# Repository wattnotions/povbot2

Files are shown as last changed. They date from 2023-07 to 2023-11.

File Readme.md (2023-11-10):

# POVbot - A Small Pi Zero FPV Robot



## 3d Print Files

Look in 3d_print folder to find a 3mf file with the chassis , camera holder and wheels ready to print.



## Software

Setting up video streaming and remote control is very easy.

Clone this repo to a raspberry pi, navigate to web_server/keyandvid/

From there run "python app.py" and the web server will start

Then you can navigate to your pis ip address using a computer on the same wifi. Use port 8000.

For example : 192.168.0.186:8000 and you should see your video stream. The robot can be steered using the WASD keys on your keyboard



## PCB Files

The hat was designed in Kicad 7. All project files are in kicad_files.

The board was made and assembled by PCBway. If you wish to get your own board assembled using PCBway look in kicad_files/pcbway_production for all of the required PCB manufacture and assembly files, ready for upload to JLCPCB.

## Youtube video

I made a short video explaining the project. It is available here:

[Watch the video](https://www.youtube.com/watch?v=tIp2PrZHXOc)

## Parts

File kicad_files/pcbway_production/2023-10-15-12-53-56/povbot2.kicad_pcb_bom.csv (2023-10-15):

designator | quantity | value | pack | mpn | mount_type
C1 | 1 | 22u | C_0603_1608Metric |  | smt
C10, C11, C12 | 3 | 22u | C_0805_2012Metric |  | smt
C13 | 1 | 10n | C_0603_1608Metric |  | smt
C2 | 1 | 0.1uF | C_0603_1608Metric |  | smt
C6, C7 | 2 | 4.7uF | C_0603_1608Metric |  | smt
C8, C9 | 2 | 10uF | C_0603_1608Metric |  | smt
D1 | 1 | LED | LED_0603_1608Metric |  | smt
D2, D3 | 2 | D_Schottky | D_SOD-323 | SBA120CS_R1_00001 | smt
J1 | 1 | GPIO | PinSocket_2x20_P2.54mm_Vertical | 61304021121 | tht
J4, J5, J6 | 3 | Conn_01x02 | JST_PH_B2B-PH-K_1x02_P2.00mm_Vertical | B2B-PH-K-S | tht
J7 | 1 | USB_B_Micro | USB_Micro-B_Molex_47346-0001 | 0473460001 | smt
L1 | 1 | 1uH | IND_SRP4020TA-1R0M | SRP4020TA-1R0M | smt
MH1, MH2, MH3, MH4 | 4 | MountingHole_2.7mm_M2.5 | MountingHole_2.7mm_M2.5 |  | tht
R1 | 1 | 1M | R_0603_1608Metric |  | smt
R5 | 1 | 470R | R_0603_1608Metric |  | smt
R6 | 1 | 2k | R_0603_1608Metric |  | smt
U1 | 1 | TPS61232DRC | Texas_S-PVSON-N10_ThermalVias | TPS61232DRCR | smt
U4 | 1 | MCP73831-2ACI_MC | SON50P200X300X100-9N | MCP73831-2ACI/MC | tht
U5 | 1 | TB6612FNG | SSOP-24_5.3x8.2mm_P0.65mm | TB6612FNG,C,8,EL | smt

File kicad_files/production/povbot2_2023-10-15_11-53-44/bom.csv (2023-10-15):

Designator | Footprint | Quantity | Value | LCSC Part #
C1 | 0603 | 1 | 22u
C10, C11, C12 | 0805 | 3 | 22u
C13 | 0402 | 1 | 10n
C2 | 0603 | 1 | 0.1uF
C6, C7 | 0603 | 2 | 4.7uF
C8, C9 | 0603 | 2 | 10uF
D1 | 0402 | 1 | LED
D2, D3 | D_SOD-323 | 2 | D_Schottky | C146335
J1 | PinSocket_2x20_P2.54mm_Vertical | 1 | GPIO
J4, J5, J6 | JST_PH_B2B-PH-K_1x02_P2.00mm_Vertical | 3 | Conn_01x02
J7 | USB_Micro-B_Molex_47346-0001 | 1 | USB_B_Micro
L1 | 0402 | 1 | 1uH
R1 | 0603 | 1 | 1M
R5 | 0603 | 1 | 470R
R6 | 0603 | 1 | 2k
U1 | Texas_S-PVSON-N10_ThermalVias | 1 | TPS61232DRC
U4 | SON50P200X300X100-9N | 1 | MCP73831-2ACI_MC | C150772
U5 | SSOP-24_5.3x8.2mm_P0.65mm | 1 | TB6612FNG | C141517

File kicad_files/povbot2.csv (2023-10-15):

Id | Designator | Footprint | Quantity | Designation | Supplier and ref | Column1 | _1
1 | C1 | C_0603_1608Metric | 1 | 22u
2 | J5,J6,J4 | JST_PH_B2B-PH-K_1x02_P2.00mm_Vertical | 3 | Conn_01x02
3 | J1 | PinSocket_2x20_P2.54mm_Vertical | 1 | GPIO
4 | D1 | LED_0402_1005Metric | 1 | LED
5 | R1 | R_0603_1608Metric | 1 | 1M
6 | C12,C10,C11 | C_0805_2012Metric | 3 | 22u
7 | J7 | USB_Micro-B_Molex_47346-0001 | 1 | USB_B_Micro
8 | D3,D2 | D_SOD-323 | 2 | D_Schottky
9 | U1 | Texas_S-PVSON-N10_ThermalVias | 1 | TPS61232DRC
10 | R5 | R_0603_1608Metric | 1 | 470R
11 | U5 | SSOP-24_5.3x8.2mm_P0.65mm | 1 | TB6612FNG
12 | C13 | C_0402_1005Metric | 1 | 10n
13 | L1 | L_0402_1005Metric | 1 | 1uH
14 | C7,C6 | C_0603_1608Metric | 2 | 4.7uF
15 | R6 | R_0603_1608Metric | 1 | 2k
16 | C2 | C_0603_1608Metric | 1 | 0.1uF
17 | U4 | SON50P200X300X100-9N | 1 | MCP73831-2ACI_MC
18 | C9,C8 | C_0603_1608Metric | 2 | 10uF

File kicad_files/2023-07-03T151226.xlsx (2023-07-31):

Index | Quantity | Part Number | Manufacturer Part Number | Description | Customer Reference | Available | Backorder | Unit Price | Extended Price EUR
1 | 2 | 2007-BB-2020BGR-TRBCT-ND | BB-2020BGR-TRB | ADDRESS LED DISCRETE SERIAL RGB |  | 2 | 0 | 1.41 | 2.82
2 | 1 | 296-44498-1-ND | TPS61232DRCR | IC REG BOOST 5V 4A 10VSON |  | 1 | 0 | 2.56 | 2.56
3 | 1 | MCP73831T-2ACI/MCCT-ND | MCP73831T-2ACI/MC | IC BATT CONTRL LI-ION 1CELL 8DFN |  | 1 | 0 | 0.72 | 0.72
4 | 1 | TB6612FNGC8ELCT-ND | TB6612FNG,C,8,EL | IC MOTOR DRIVER 2.7V-5.5V 24SSOP |  | 1 | 0 | 1.84 | 1.84
5 | 1 | 38-1007-ND | D6505I | LASER DIODE 650NM 5MW TO18 |  | 1 | 0 | 11.09 | 11.09
6 | 1 | 1528-2688-ND | 3872 | 5V ELECTROMAGNET 2.5 KG HOLDING |  | 1 | 0 | 6.85 | 6.85
7 | 3 |  | 2132260210 | Molex clik mate smd ra 2 way
8 | 2 |  | 151350200 (https://www.digikey.ie/en/products/detail/molex/0151350200/6833461) | click mate pre made leads

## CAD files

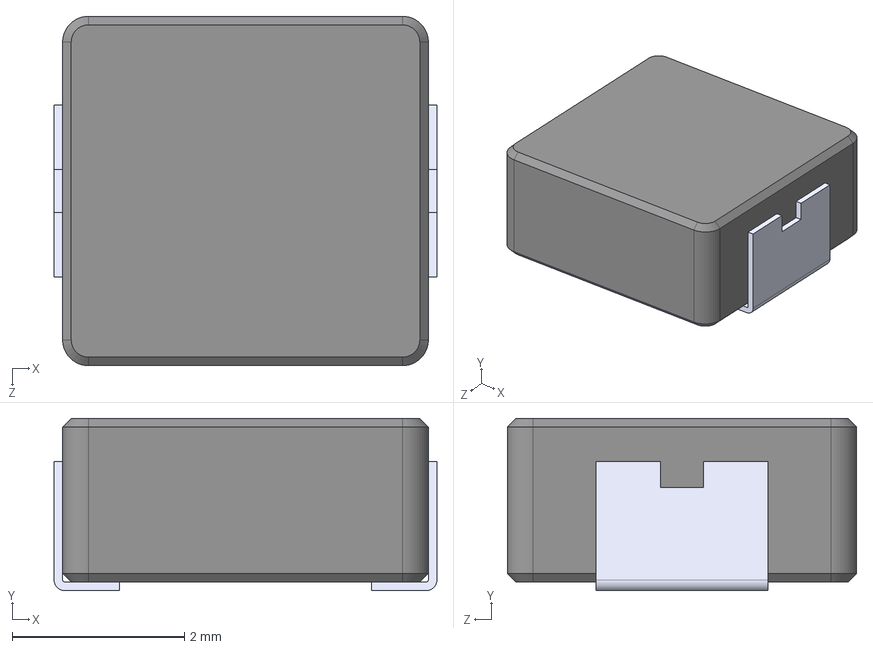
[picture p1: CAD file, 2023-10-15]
kicad_files/SRP4020TA-1R0M/SRP4020TA-1R0M.step
4.45 x 2.00 x 4.06 mm

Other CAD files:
3d_print/povbot_3d_print.3mf

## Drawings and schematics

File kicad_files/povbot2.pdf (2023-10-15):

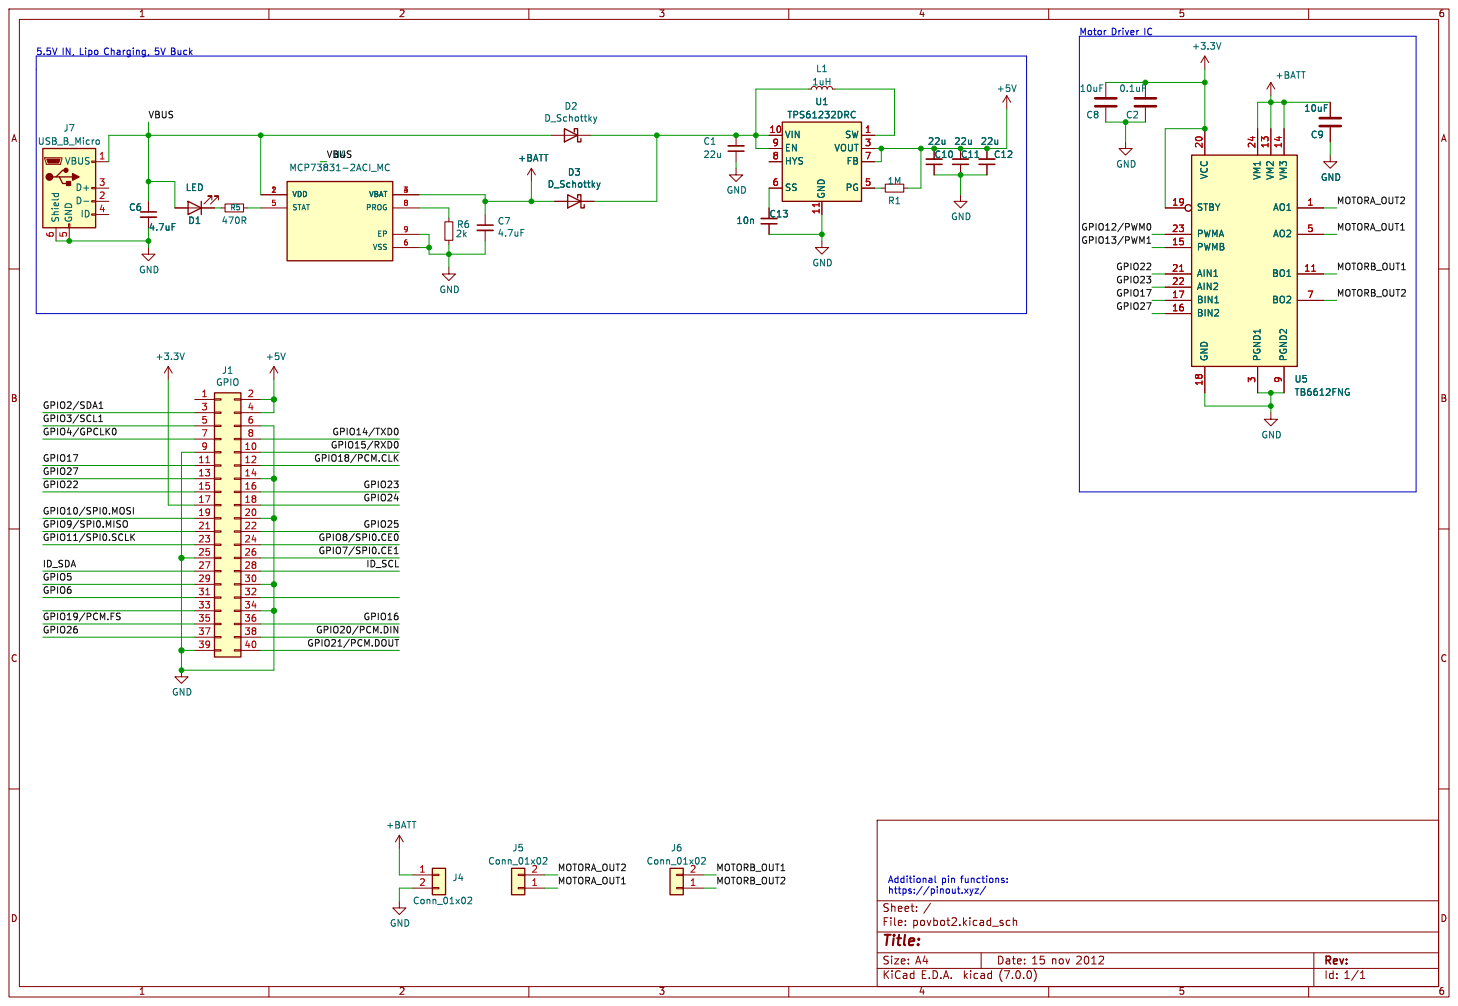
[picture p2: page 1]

Id: 1/1 Title: File: povbot2.kicad_sch Sheet: /

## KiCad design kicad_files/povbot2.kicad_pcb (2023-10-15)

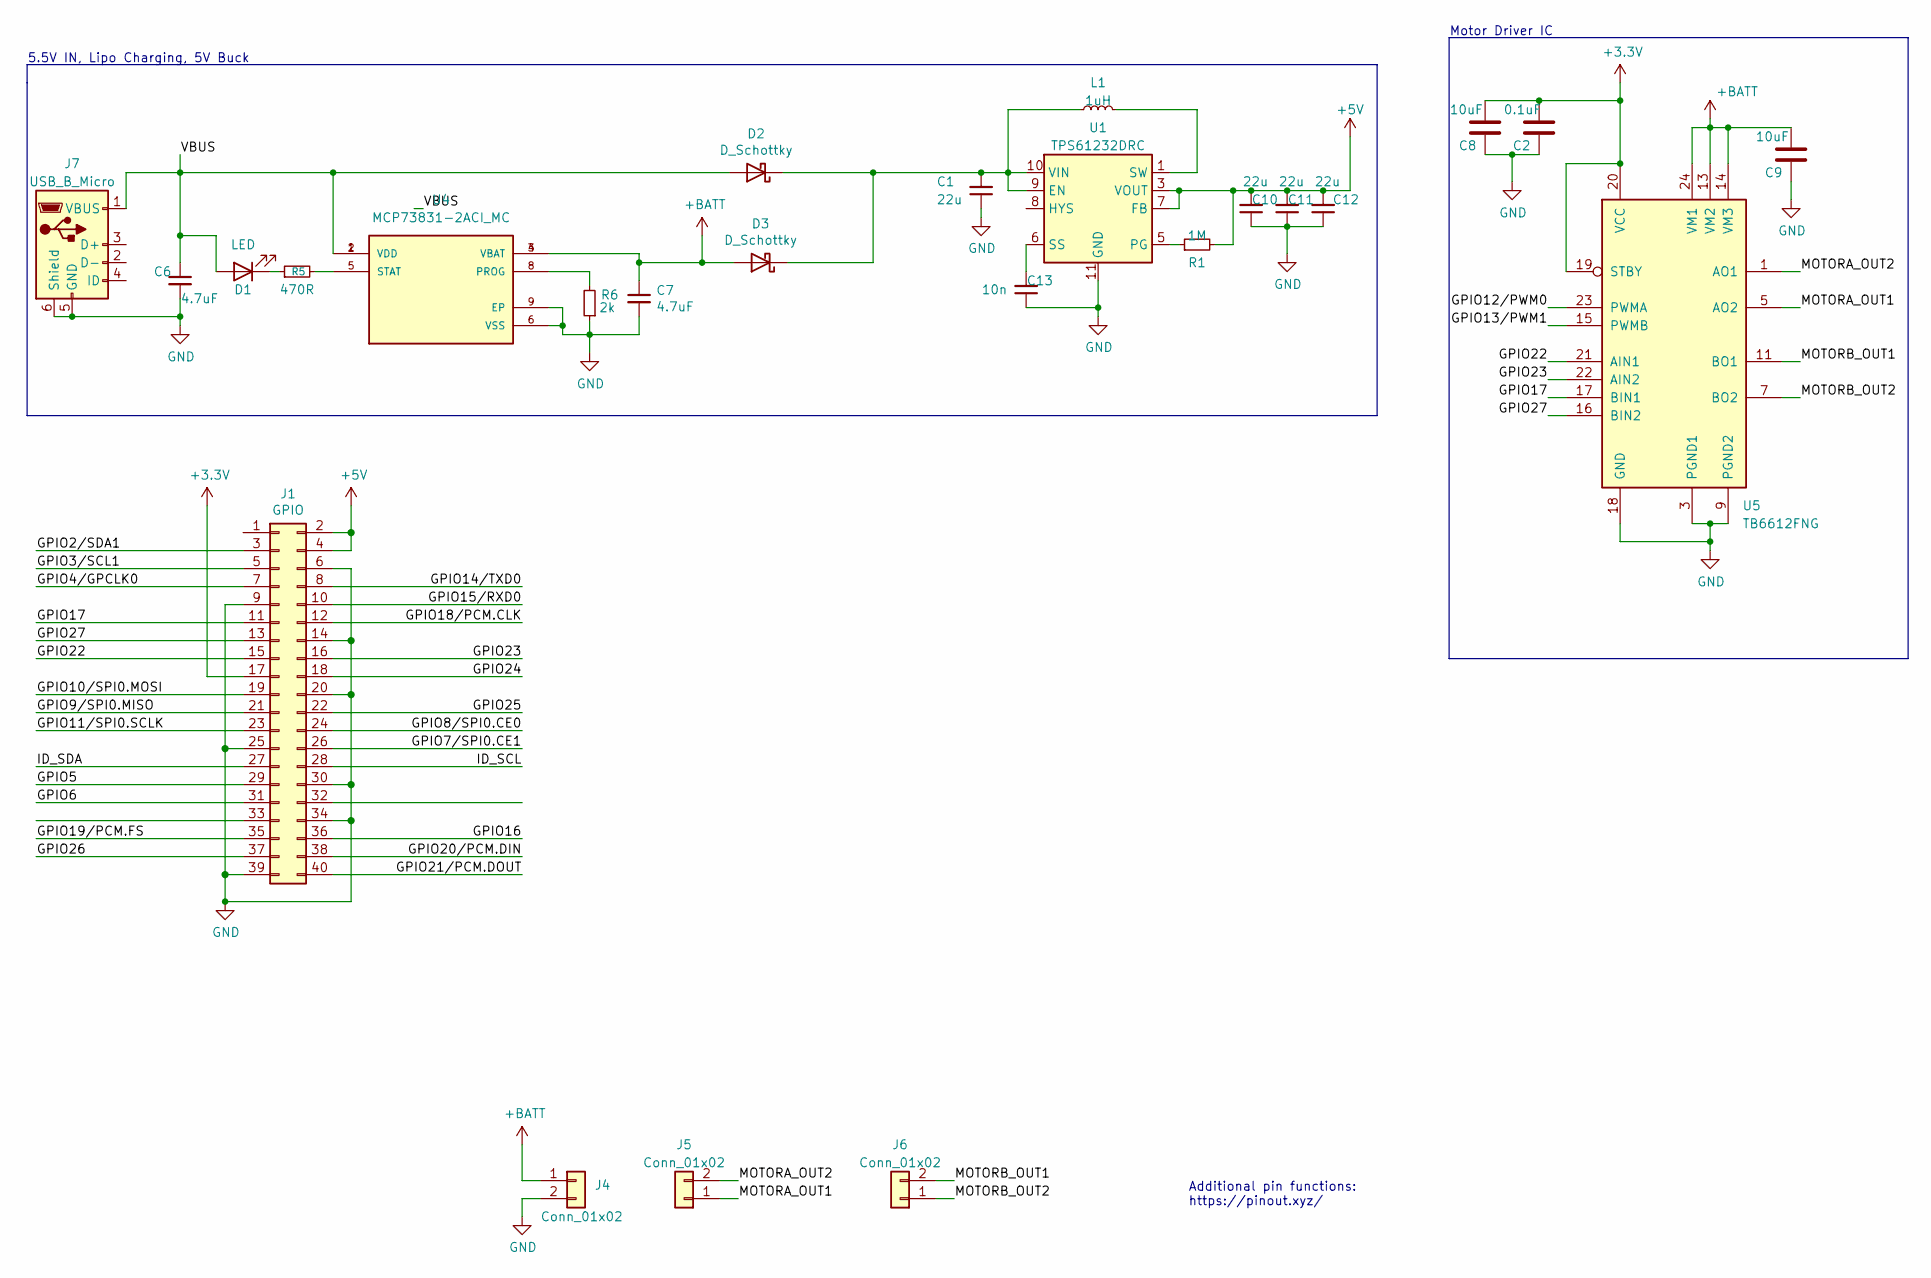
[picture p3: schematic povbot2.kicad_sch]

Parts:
C1: 22u; C_0603_1608Metric
C2: 0.1uF; C_0603_1608Metric
C6, C7: 4.7uF; C_0603_1608Metric
C8, C9: 10uF; C_0603_1608Metric
C10, C11, C12: 22u; C_0805_2012Metric
C13: 10n; C_0603_1608Metric
D1: LED; LED_0603_1608Metric
D2, D3: D_Schottky; D_SOD-323; MPN SBA120CS_R1_00001; LCSC C146335
J1: GPIO; PinSocket_2x20_P2.54mm_Vertical; MPN 61304021121
J4, J5, J6: Conn_01x02; JST_PH_B2B-PH-K_1x02_P2.00mm_Vertical; MPN B2B-PH-K-S
J7: USB_B_Micro; USB_Micro-B_Molex_47346-0001; MPN 0473460001
L1: 1uH; IND_SRP4020TA-1R0M; MPN SRP4020TA-1R0M
R1: 1M; R_0603_1608Metric
R5: 470R; R_0603_1608Metric
R6: 2k; R_0603_1608Metric
U1: TPS61232DRC; Texas_S-PVSON-N10_ThermalVias; MPN TPS61232DRCR
U4: MCP73831-2ACI_MC; SON50P200X300X100-9N; PARTREV G; LCSC C150772
U5: TB6612FNG; SSOP-24_5.3x8.2mm_P0.65mm; MPN TB6612FNG,C,8,EL; LCSC C141517

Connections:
+3V3: C2.1, C8.1, J1.17, U5.19 (STBY), U5.20 (VCC)
+5V: C10.2, C11.2, C12.2, J1.2, J1.4, R1.2, U1.3 (VOUT), U1.4 (VOUT), U1.7 (FB)
+BATT: C7.1, C9.1, D3.2 (A), J4.1, U4.3 (VBAT), U4.4 (VBAT), U5.13 (VM2), U5.14 (VM3), U5.24 (VM1)
/GPIO2/SDA1: J1.3
/GPIO3/SCL1: J1.5
/GPIO4/GPCLK0: J1.7
/GPIO5: J1.29
/GPIO6: J1.31
/GPIO7/SPI0.CE1: J1.26
/GPIO8/SPI0.CE0: J1.24
/GPIO9/SPI0.MISO: J1.21
/GPIO10/SPI0.MOSI: J1.19
/GPIO11/SPI0.SCLK: J1.23
/GPIO12/PWM0: U5.23 (PWMA)
/GPIO13/PWM1: U5.15 (PWMB)
/GPIO14/TXD0: J1.8
/GPIO15/RXD0: J1.10
/GPIO16: J1.36
/GPIO17: J1.11, U5.17 (BIN1)
/GPIO18/PCM.CLK: J1.12
/GPIO19/PCM.FS: J1.35
/GPIO20/PCM.DIN: J1.38
/GPIO21/PCM.DOUT: J1.40
/GPIO22: J1.15, U5.21 (AIN1)
/GPIO23: J1.16, U5.22 (AIN2)
/GPIO24: J1.18
/GPIO25: J1.22
/GPIO26: J1.37
/GPIO27: J1.13, U5.16 (BIN2)
/ID_SCL: J1.28
/ID_SDA: J1.27
/MOTORA_OUT1: J5.1, U5.5 (AO2), U5.6 (AO2)
/MOTORA_OUT2: J5.2, U5.1 (AO1), U5.2 (AO1)
/MOTORB_OUT1: J6.2, U5.11 (BO1), U5.12 (BO1)
/MOTORB_OUT2: J6.1, U5.7 (BO2), U5.8 (BO2)
/VBUS: C6.1, D1.2 (A), D2.2 (A), J7.1 (VBUS), U4.1 (VDD), U4.2 (VDD)
GND: C1.1, C2.2, C6.2, C7.2, C8.2, C9.2, C10.1, C11.1, C12.1, C13.1, J1.6, J1.9, J1.14, J1.20, J1.25, J1.30, J1.34, J1.39, J4.2, J7.5 (GND), J7.6 (Shield), R6.1, U1.11 (GND), U4.6 (VSS), U4.9 (EP), U5.3 (PGND1), U5.4 (PGND1), U5.9 (PGND2), U5.10 (PGND2), U5.18 (GND)
unnamed: D1.1 (K), R5.1
unnamed: C1.2, D2.1 (K), D3.1 (K), L1.1, U1.9 (EN), U1.10 (VIN)
unnamed: L1.2, U1.1 (SW), U1.2 (SW)
unnamed: R1.1, U1.5 (PG)
unnamed: C13.2, U1.6 (SS)
unnamed: R6.2, U4.8 (PROG)
unnamed: R5.2, U4.5 (STAT)

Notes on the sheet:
Motor Driver IC
5.5V IN, Lipo Charging, 5V Buck
Additional pin functions: https://pinout.xyz/

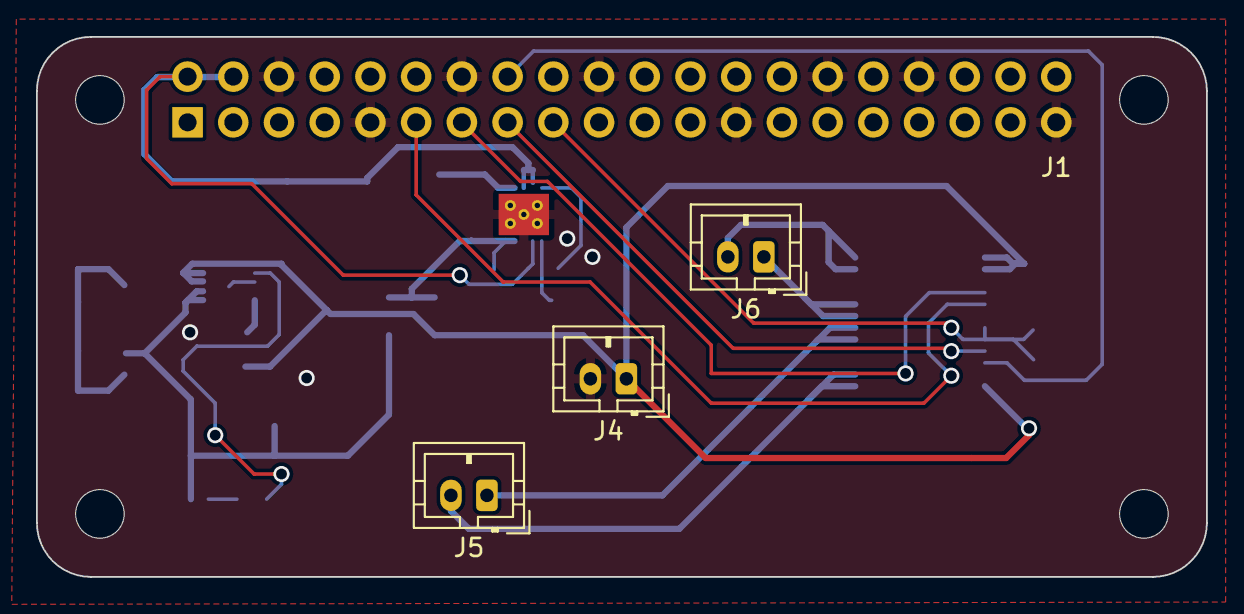
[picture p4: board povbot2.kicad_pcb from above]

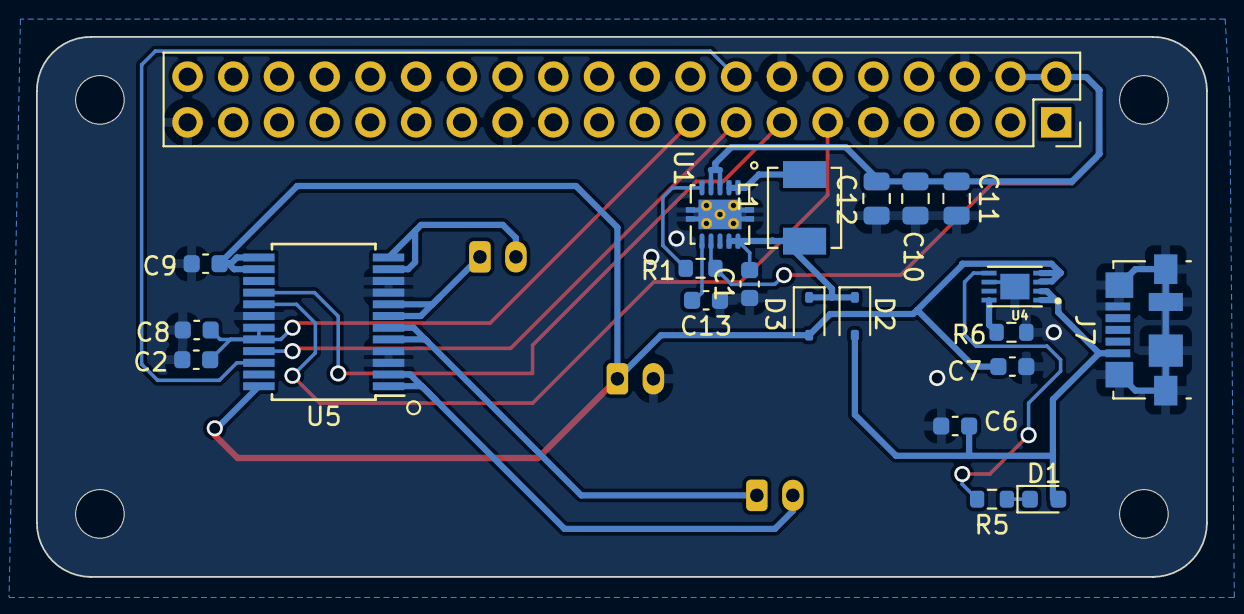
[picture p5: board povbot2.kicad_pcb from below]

Board: 2 copper layers, 65.0 x 30.0 mm, 29 parts (22 on the bottom side), 20 nets.

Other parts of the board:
MH1, MH2, MH3, MH4: MountingHole_2.7mm_M2.5

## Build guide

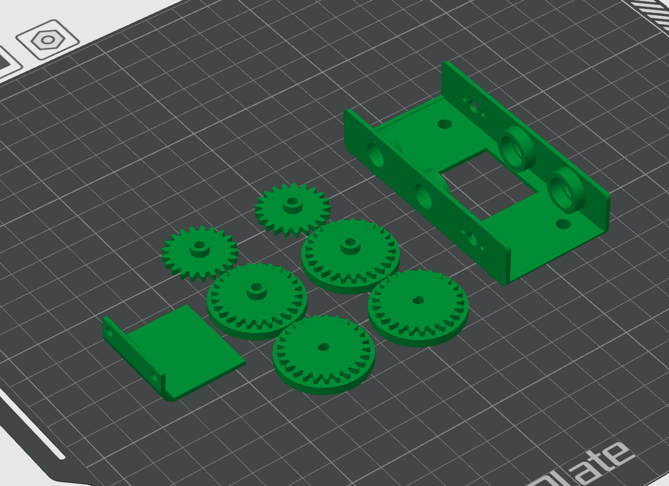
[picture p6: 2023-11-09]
3d_print/3d-print-preview.png

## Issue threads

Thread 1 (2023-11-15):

Extra information request.

derekmulcahy, 2023-11-15:
Hi,

What a great little robot, thanks for sharing!

I have some questions about the parts used to construct the robot.

What size are the bearings?
What type of battery did you use and where did you hide it?
The motors are available with a variety of gears and different RPM specs. Which did you use?

Cheers,
Derek

MatjazSi, 2023-11-22:
Hi, I would also like tho know the answers to the above questions.
Also, would it be possible to get the Autodesk Fusion file?

Best wishes,
Matjaz

DavidLongley, 2023-11-25:
Hello,

Cool project. I have one issue with the code as it is not streaming the video. I get a broken link icon. The test script (vid_serve_example.py) works fine. Any ideas?
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

Regards,
David

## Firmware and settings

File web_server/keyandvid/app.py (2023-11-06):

from flask import Flask, render_template, request, Response
import threading
import RPi.GPIO as GPIO
import io
import picamera
import logging
from flask_cors import CORS
from threading import Condition
app = Flask(__name__)
CORS(app)  # This will enable CORS for all routes

GPIO.setmode(GPIO.BCM)
GPIO.setup(22, GPIO.OUT)
GPIO.setup(23, GPIO.OUT)
GPIO.setup(17, GPIO.OUT)
GPIO.setup(27, GPIO.OUT)


GPIO.output(22, GPIO.LOW)
GPIO.output(23, GPIO.LOW)
GPIO.output(17, GPIO.LOW)
GPIO.output(27, GPIO.LOW)

def forward():
    GPIO.output(22, GPIO.LOW)  #left side
    GPIO.output(23, GPIO.HIGH)
    
    GPIO.output(17, GPIO.HIGH) #right side
    GPIO.output(27, GPIO.LOW)
    
def stop():
    GPIO.output(22, GPIO.LOW)  
    GPIO.output(23, GPIO.LOW)
    
    GPIO.output(17, GPIO.LOW) 
    GPIO.output(27, GPIO.LOW)
    
def right():
    GPIO.output(22, GPIO.LOW)  
    GPIO.output(23, GPIO.HIGH)
    
    GPIO.output(17, GPIO.LOW) 
    GPIO.output(27, GPIO.HIGH)
    
def left():
    GPIO.output(22, GPIO.HIGH)  
    GPIO.output(23, GPIO.LOW)
    
    GPIO.output(17, GPIO.HIGH) 
    GPIO.output(27, GPIO.LOW)



@app.route('/key', methods=['GET'])
def get_key():
    key = request.args.get('key')
    if key:
        print(f'Key Pressed: {key}')
        # Check which key is pressed and set GPIO pins accordingly
        if key == 'W':
            forward()
        elif key == 'A':
            left()
        elif key == 'S':
            stop()
        elif key == 'D':
            right()
    return '', 200

@app.route('/')
def index():
    """Video streaming home page."""
    return render_template('index.html')

def gen():
    """Video streaming generator function."""
    with picamera.PiCamera(resolution='640x480', framerate=24) as camera:
        camera.rotation = 270  # Rotate the camera stream by 90 degrees counter-clockwise
        output = StreamingOutput()
        camera.start_recording(output, format='mjpeg')
        try:
            while True:
                with output.condition:
                    output.condition.wait()
                    frame = output.frame
                yield (b'--frame\r\n'
                       b'Content-Type: image/jpeg\r\n\r\n' + frame + b'\r\n\r\n')
        finally:
            camera.stop_recording()

@app.route('/video_feed')
def video_feed():
    """Video streaming route. Put this in the src attribute of an img tag."""
    return Response(gen(),
                    mimetype='multipart/x-mixed-replace; boundary=frame')

class StreamingOutput(object):
    def __init__(self):
        self.frame = None
        self.buffer = io.BytesIO()
        self.condition = Condition()

    def write(self, buf):
        if buf.startswith(b'\xff\xd8'):
            # New frame, copy the existing buffer's content and notify all
            # clients it's available
            self.buffer.truncate()
            with self.condition:
                self.frame = self.buffer.getvalue()
                self.condition.notify_all()
            self.buffer.seek(0)
        return self.buffer.write(buf)

if __name__ == '__main__':
    app.run(host='0.0.0.0', port=8000, threaded=True)

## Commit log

2023-07-03 added motor driver IC, BOM, laser diode, LEDs, and electomagnet
    [2023-07-03T151226.xlsx, povbot2.kicad_pcb, povbot2.kicad_sch]
2023-07-31 started pcb, added foorprints etc
    [2023-07-03T151226.xlsx, povbot2.kicad_pcb]
2023-08-02 floorplanning done
    [povbot2.kicad_pcb, povbot2.kicad_sch]
2023-10-15 changed inductor larger package 5A current version, made pcbway fab files
    [SRP4020TA-1R0M.step, bom.csv, designators.csv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]
2023-11-04 working vid with remote control buttons
2023-11-09 added 3mf print file
    [povbot_3d_print.3mf]
2023-11-09 cleaned up dir structure
    [2023-07-03T151226.xlsx, SRP4020TA-1R0M.step]
